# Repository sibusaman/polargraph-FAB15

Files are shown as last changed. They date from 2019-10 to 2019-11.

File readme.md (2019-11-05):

# Machines for Learning : The Wall Plotter
### **[Funded by The Hamdan Foundation, UAE](http://www.ha.ae/en/web/guest/home)**

During FAB15, 12 machines were built by the FabLab community and donated to 12 schools in Egypt. We made 
- 2 x mini CNC mill
- 5 x 3D printer
- 5 x Wall Plotter
  
The project was Funded by **[The Hamdan Foundation, UAE](http://www.ha.ae/en/web/guest/home)**.

The wall plotter design is mostly based on the [PolarGraph](http://www.polargraph.co.uk) machine. Here we document the slight differences in the design, the assembly instruction, software setup, calibration steps and other trouble shooting steps.

The machine was delivered in fully assembled and in fully working condition. Also the machine is very simple in terms of mechanical complexity. Which means detailed assembly instruction won't be necessary, as it is very trivial once the machine is in hand. The end users are supposed to hack these machines, modify, redesign..., so, we have provided some crucial information to help the end user do so. 

# Hardware

## BOM

The BOM is only for assembly, the end user do not need these as they already got the machine fully assembled.

- 2 x Nema 17 Bi-Stepper Motors 12v
- GT2 Timing belt, length depends on the machine dimension
- GT2 Pulley
- 1 x 9g 0-180 degree  Servo Motor, 
- 1 x Arduino Uno
- 1 x [CNC-Shield v3](https://blog.protoneer.co.nz/arduino-cnc-shield)
- 2 x Pololu, step-dir stepper driver or compatible
- A few jumpers (not wires), usually comes with stepper driver or CNC-shield
- 1 x 12v Power supply and 3-core power cable  
- Sufficient length of quality wire for 12v DC
- Wires for extending the stepper and servo motors.
- .
- m3,m4 and m6 nuts, washers and bolts of various lengths
- m15 washers or bolts or something similar to use as weights.
- zip-ties
- 3-5mm plywood sheet for laser cutting
- 12mm or more thick plywood/MDF sheet or similar. Dimension corresponds to the dimension of the final machine.
- Access to a 3D printer as there are a few 3D printed parts- 

## Mechanical Assembly 
- **Mounting the timing belt to the gondola :** The timing belt has to be attached with the Gondola by pinching the belt between the pen-holder (it has a small tooth corresponding to the timing belt tooth) and a small securing laser-cut retainer.
  - **The retainer** retainer
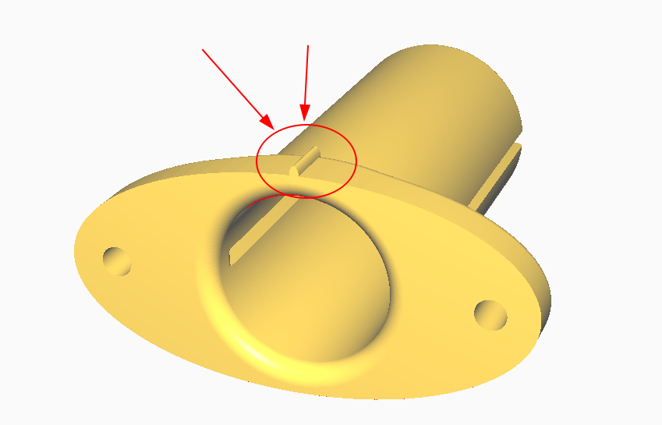
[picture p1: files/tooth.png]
tooth
  - **The tooth on the pen holder** 
  
- **Mounting the stepper motor :**  The stepper motor is mounted on a laser cut plywood. This assembly then goes onto the MDF/Plywood panel(used as the drawing board). 
  - If the laser cut plates are too flimsy, you may stack two of them.

  - The motor, in our case, is mounted to the plate using **m3** screws. It is recommended to use m3 washer, especially if you use soft plywood for the stepper mount plate.
  
  - The plate is then mounted to the big board using m5/m6 bolts, washers on both sided and nuts. 
  
  - There are alignment guides on the plates, there is a tiny hole to locate the corner of the board. Align this hole to the corner of the board. See the picture below.
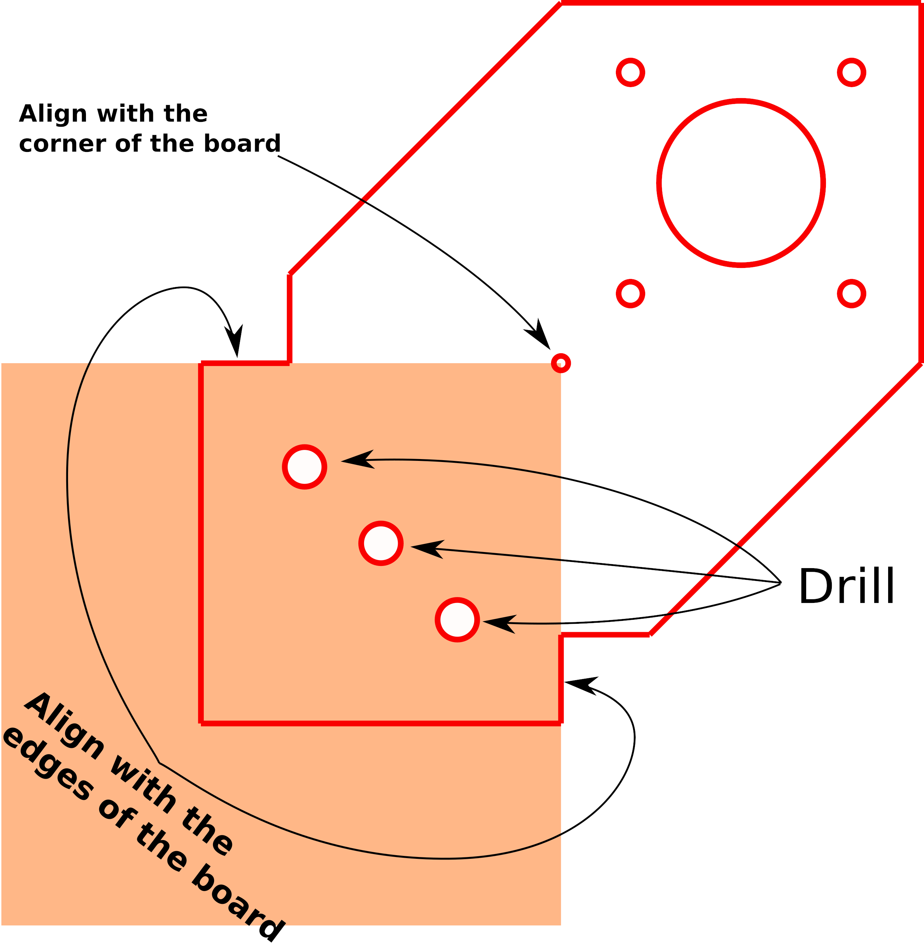
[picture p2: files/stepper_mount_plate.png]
stepper-plate
  - 
  
  - Then there are two right angle cuts, align these to the board edges. With these done, clamp the plate and drill the mounting holes on  the board. See the picture above.
  
- **Mounting the servo motor :**  The servo motor mount is designed to be used with small zip-ties. There are two sets of mounting holes. 
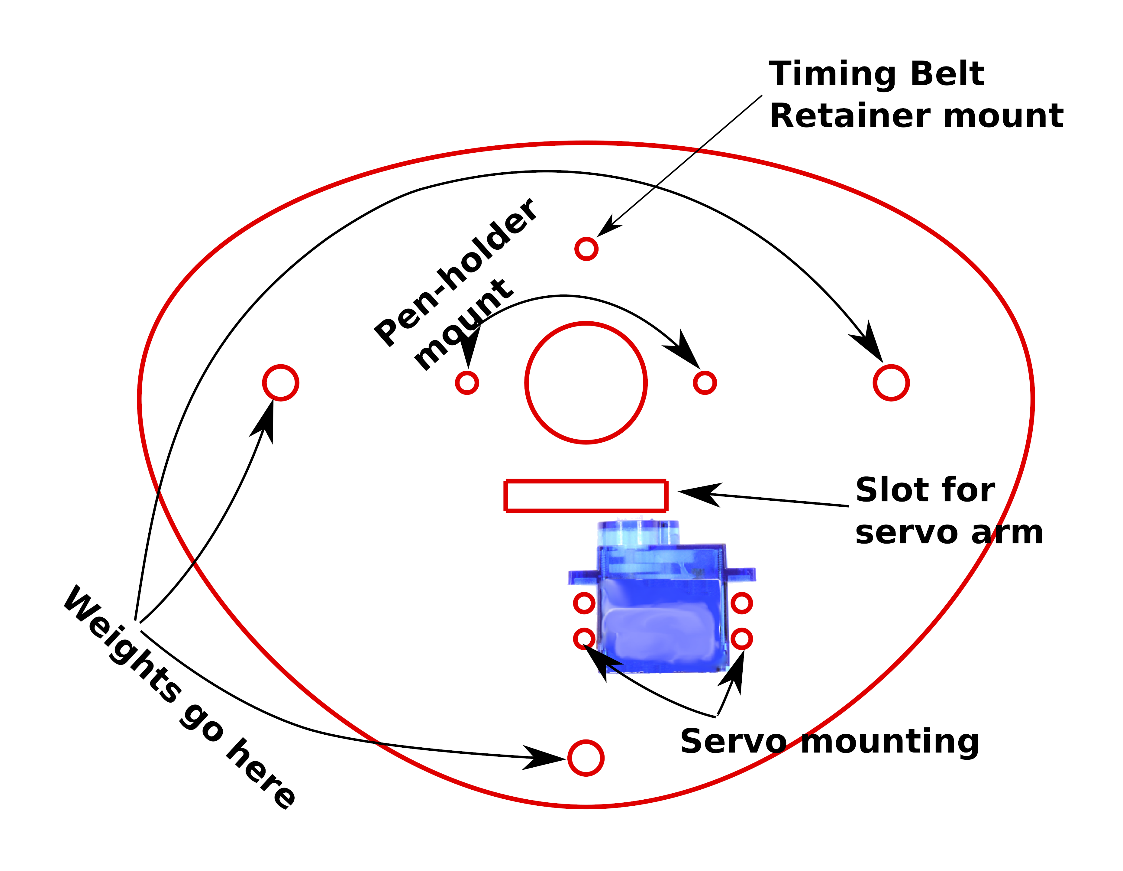
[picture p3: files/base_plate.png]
- 
  - The arm used is the single cam type.
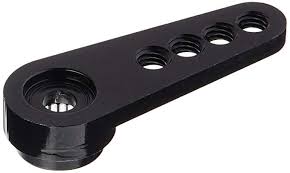
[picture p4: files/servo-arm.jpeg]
servo arm
  -  

  - **Mounting the servo arm** : Assuming that you have a 0-180 servo, not the continues rotation type. Connect the machine and do 'PEN-UP', at this position the arm should be mounted such that the arm touches the paper, raising the pen so that it doesn't touch the paper.  

  - If you have different types of servos you will have to play around and find the correct values for the PEN-UP and PEN-DOWN and edit the configuration file.

- **Attaching the counterweights :** There are three weights on the system. Two on either side. And one on the GOndola itself. 
  - The quick and dirty(and cheap) way I found to make a tunable counterweight is those 500ml water-bottles. The amount of the water tunes the weight. These are only for the ones on the side.

  - This can be done by making a small slit (with a sharp blade of course) on the cap, and inserting the timing belt through it. It will hold on it's on if you make the slit clean and just enough for the belt to enter through.

  - For the weight on the Gondola, it is recommended to use heavy steel nuts. This is clean and compact.

  - There are three place where you can mount these nuts on the gondola. One on the bottom and two on the sides. 
  **See the picture above**   

  - The long bolts used for mounting these nuts are actually thinner (**m5** or **m6**) than the nuts itself(often **m16** and higher, as  they are heavy). Because the bolt is mounted upside down and if we use **m16** bolt the head of this bolt will be too thick for the servo arm to be able to lift the pen. You can use m16 bolts, but then you will have to use longer servo arms and tune the servo parameters.

  - To secure the **m16** nuts on the thin bolts, you may cut washers from plywood.

- **Mounting the pen :** The pen holder will have to be modified for the pen you use, or  you will have to use some sort of grippy spacers, preferably rubber. You can also use rubber bands to increase the grip on the pen. The pen has to be mounted such that the tip just lifts up when the servo arm is engaged (pen-up position). [Here is the STL of the pen holder](./files/pen_holder.stl)
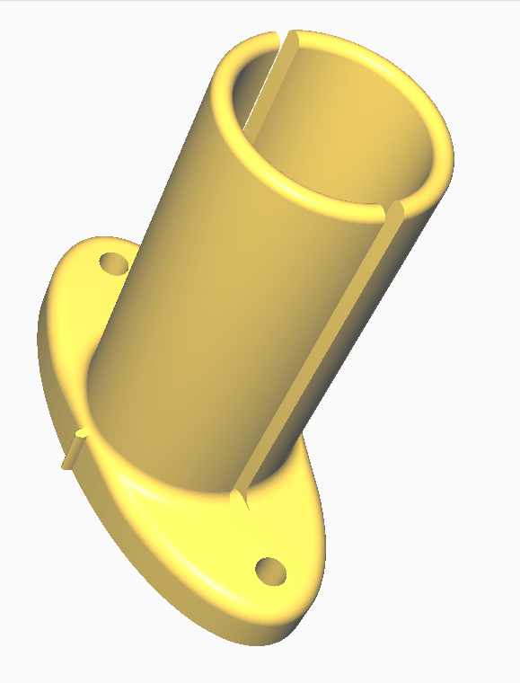
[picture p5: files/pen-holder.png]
pen-holder
- 

## Electronics 

### Connections
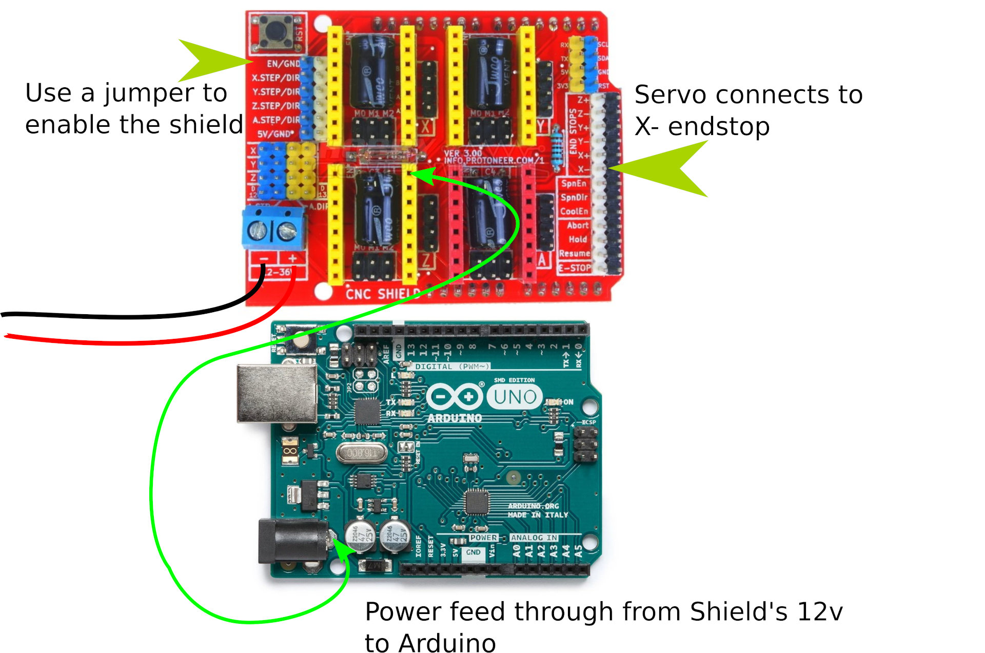
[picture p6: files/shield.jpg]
connections
- 
- **Servo connection :** The servo Wire need to be extended with Flat-Flexible-Cable FFC. The servo signal wire goes to the **PIN-9** of the arduino or **x- end-stop** in the shield. 

- **Micro-Stepping :** You can enable micro-stepping (I did, 1/16) for better resolution. 
- Stepper also need to be extended, but with wires that are rated for the maximum stepper current rating. Ethernet cables are cheap and readily available option. You get four pairs of wire from an ethernet cable, enough for both of the stepper motors. 

I used X and Y ports in the shield.

### Configuration
- **Enable jumper on CNC shield :** See the picture above. 

- **Power pass through from  CNC shield to Arduino :** See the picture above. This is required as the servo is powered by the 5v rail, which in turn comes from the Arduino board. The 500mA from the USB is insufficient to power the servo too.
 
  - This can be done with a wire with a male connector in one end, which connects to the **V_mot** pin of one of the unused stepper driver slots. The other end can be soldered to the positive out of the barrel connector, before the protection circuitry in Arduino.

  - Alternatively you can also split the 12v line, use a **5.5/2.1mm** barrel connector 

# Software

All the necessary files can be found in the repository. The Micro-controller firmware and Application can be found inside this [zip file](./files/Polargraph-2017-11-01.zip).

## Firmware and Tweaks

The folder, ```arduino-source``` have the firmware source.
Open it and copy the contents of the ```libraries```  into your arduino library folder (in linux, by default it is in ~/Arduino/libraries).

Also copy the ```polargraph_server_a1``` folder into the arduino project folder (````~/Arduino```` in linux).

There are few important edits to be made. 

- ```polargraph_server_a1.ino```
  - define the microcontroller (we have an UNO)
    - uncomment ```#define MICROCONTROLLER MC_UNO``` 
  - Choose the stepper driver type (we use pololu)
    - uncomment ```#define SERIAL_STEPPER_DRIVERS```
  - Disable unused features (optional)
  - define serial speed (57600 bps by default)
  - servo pin (we used default PIN9)
    - ```const byte PEN_HEIGHT_SERVO_PIN = 9;```
- ```configuration.ino```
  - step and direction pins for the controller
    ```bash
    #ifdef SERIAL_STEPPER_DRIVERS
   
    #define MOTOR_A_ENABLE_PIN 8
    #define MOTOR_A_STEP_PIN 2
    #define MOTOR_A_DIR_PIN 5
  
    #define MOTOR_B_ENABLE_PIN 8
    #define MOTOR_B_STEP_PIN 3
    #define MOTOR_B_DIR_PIN 6
    AccelStepper motorA(1,MOTOR_A_STEP_PIN, MOTOR_A_DIR_PIN); 
    AccelStepper motorB(1,MOTOR_B_STEP_PIN, MOTOR_B_DIR_PIN); 
    #endif
    ```

## Application and configuration
There is an UI for this machine and the application can be found inside the zip. The app is written an compiled using [processing 2.2.1](https://processing.org/download/). It does not work in version 3+.

The source code and pre-compiled binaries for Linux (and Windows, but I haven't tested this) are also provided in the zip.

The controller directory inside the zip have the compiled binary for the UI for the machine, for linux and windows. The default configuration file is named default.properties.txt, this can be replaced with custom config file. 

### Launching application
In linux, you need to make the ```polargraphcontroller``` file located in ```Polargraph-2017-11-01/controller/application.linux64/``` executable, by

```bash
chmod +x polargraphcontroller
```
Then launch the application by
```bash
./polargraphcontroller
```

### Loading custom config file 
The text file, [polar_custom.properties.txt](./files/polar_custom.properties.txt) is the configuration file for the UI and some aspects of the machine. There is a default config file, you can either replace it with the custom config file (and rename it) or load the custom file every-time you launch the application.
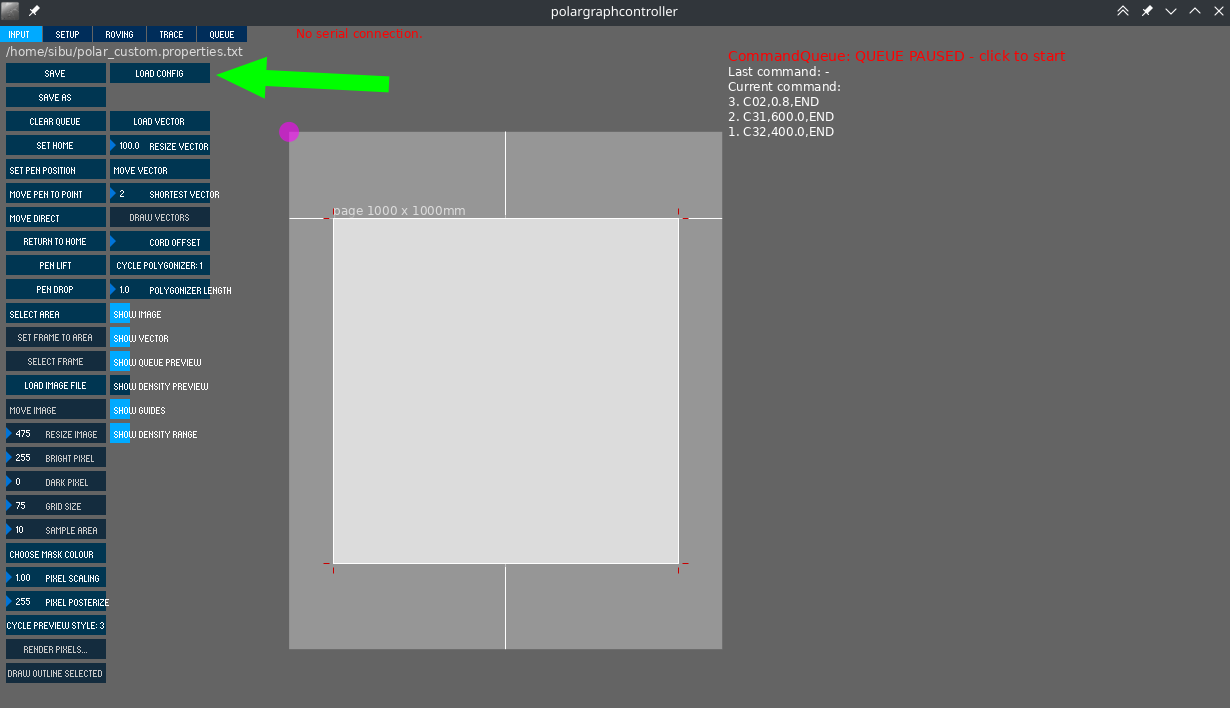
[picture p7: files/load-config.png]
config


        Note: Many of the machine configuration settings can be changed permanently by editing the polargraph_server_a1.ino , but still can be overridden by user configuration file. 

        Also the user configuration can be written to the micro-controller EEPROM from the application.

# Calibration and Tuning

## Calculating Steps/Rev
    Number of Steps to be sent to the step-direction based stepper controller for a full rotation of the shaft. 

This depends on the three parameters, 
- Micro-Stepping settings of the driver
- Number of full steps per rotation of the stepper motor, as specified in the motor specifications.
- Gear ratio if any

In our case we do not have any gear in the assembly, it's direct drive. So if the drivers are configured to be **1/N** Micro-Stepping, and the Motor is rated for **M** steps per rotation, 

**Steps/Rev = M x N**

    For our system this number is 200 x 16 = 3200 Steps/Rev

## Calculating mm/Rev
    This is the linear motion by the drive belt/string per rotation of the motor. In essence, it is the effective circumference of the final drive gear/pulley

For a system with timing belt,
This number depends on the number of gear pitch and number of gears on the drive pulley. 

**(Pitch) x (Number of gear on the drive gear)**

    For our system, we are using a 20 tooth GT2 pulley to drive the GT2 belt, so, this number is 20 x 2 = 40mm/Rev

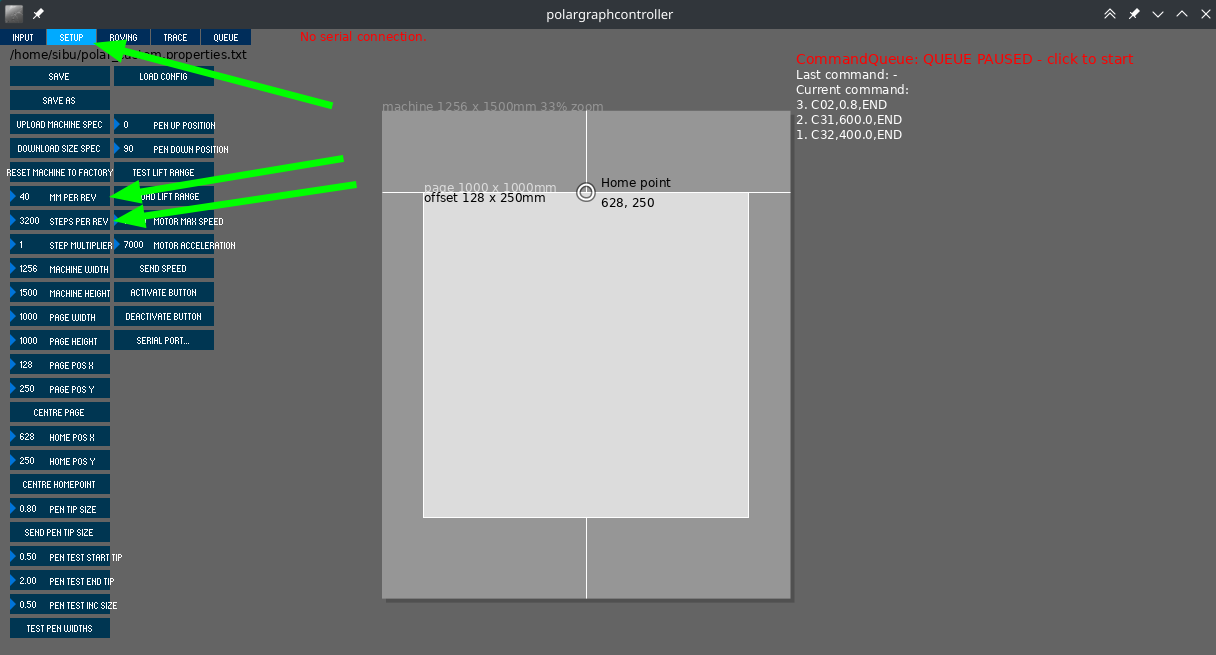
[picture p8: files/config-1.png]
config-1
 
 You can change the defaults in the configuration file.

## Max speed and acceleration 
The max speed and acceleration is to be found out by the user and it varies from machine to machine. It depends on several factors like, 

- The Torque rating of the motor

- Power-supply 

  - supplying 12v to to a 24v rated motor won't give you the ideal performance

- Stepper motor controller

- Micro-stepping configuration

- The tensioning weights used 

  - more weight means less acceleration for a given torque
  
  - but, less weight will make the belt slip from the gear
  
  - less weight also means less pen force.

These parameters can be found by trial and error. The crude way os to find the settings at which it fails and turn it down a bit.

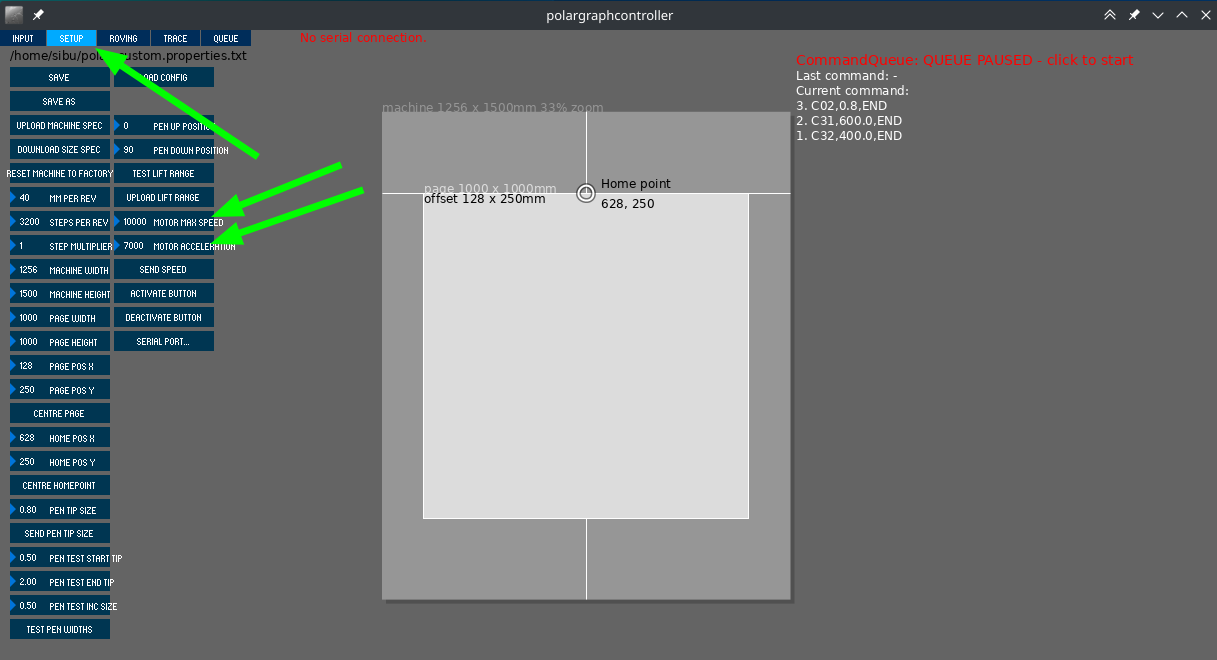
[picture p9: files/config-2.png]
config-2
 

## Setting zero

**This could be the most crucial step of the entire assembly.** Where you set the origin in the machine is super important in polar machines to make the machine where move the way you want. Read the note below to understand why.

    Note: The important thing to understand is that the machine is working in polar coordinates. 
    
    Let's call 
    - X and Y as the machine head position.
    - dx and dy as the change in X and Y we need
    - m1 and m2 as the rotation in motor 1 and 2 to make the change dx and dy.
    
    In traditional cartesian coordinates, no matter where your head is at you can ask the machine to move dx and dy and it will move exactly dx and dy. In a way in cartesian machines the motion of the head is only a function of the motion of the motor shafts, m1 and m2 and not the current positions itself.

    Even in unconventional cartesian machines like H-bot or CORE-XY, the dx and dy is only a function of m1 and m2.

    dx,dy = f(m1,m2)

    But for polar machines like this. dx and dy is a function of m1,m2,X and Y

    dx,dy = f(m1,m2,X,Y)

As you see in the note above, in this machine calibration is extremely important, else you will get a distorted drawing. For example, you may want to draw a square and if your calibration is wrong, you may end up with some wired shape with curved edges.

There are few measurements and configuration settings you have to do before setting zero.

We need to measure the 
- **Machine dimension (Width and Height) :**  
  - **The width** of the machine is measured from the left anchor point of the belt to the right anchor point of the belt. we can approximate this by **shaft to shaft** length. 
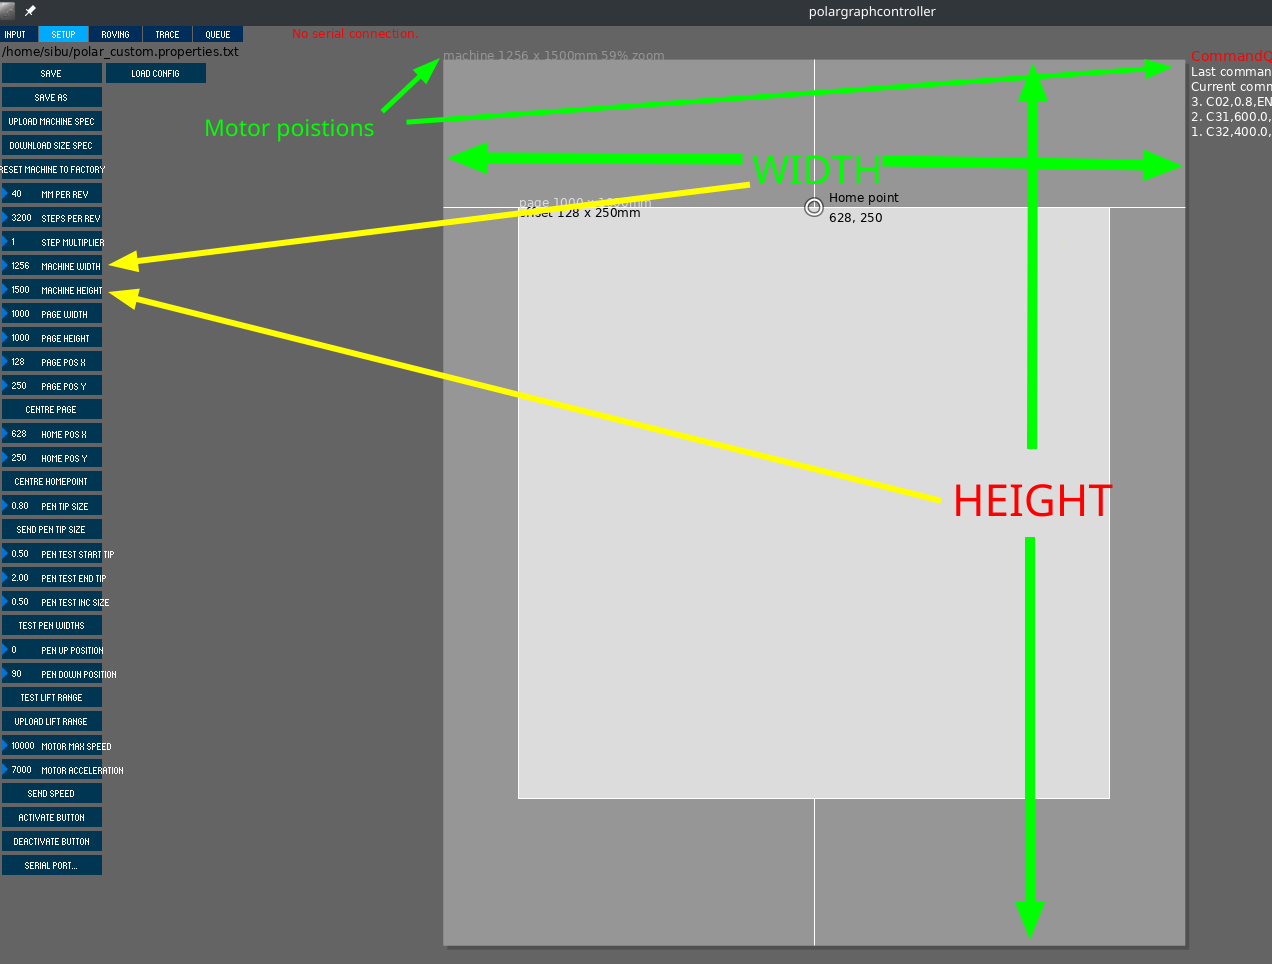
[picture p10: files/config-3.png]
config-3
    - 

  - The height of the machine is not that critical, means it doesn't affect the performance of the machine. But set it as the height of the MDF/Plywood drawing platform.

- **Page Dimensions :** This is the WIdth and Height of the page/paper in which we are drawing. 
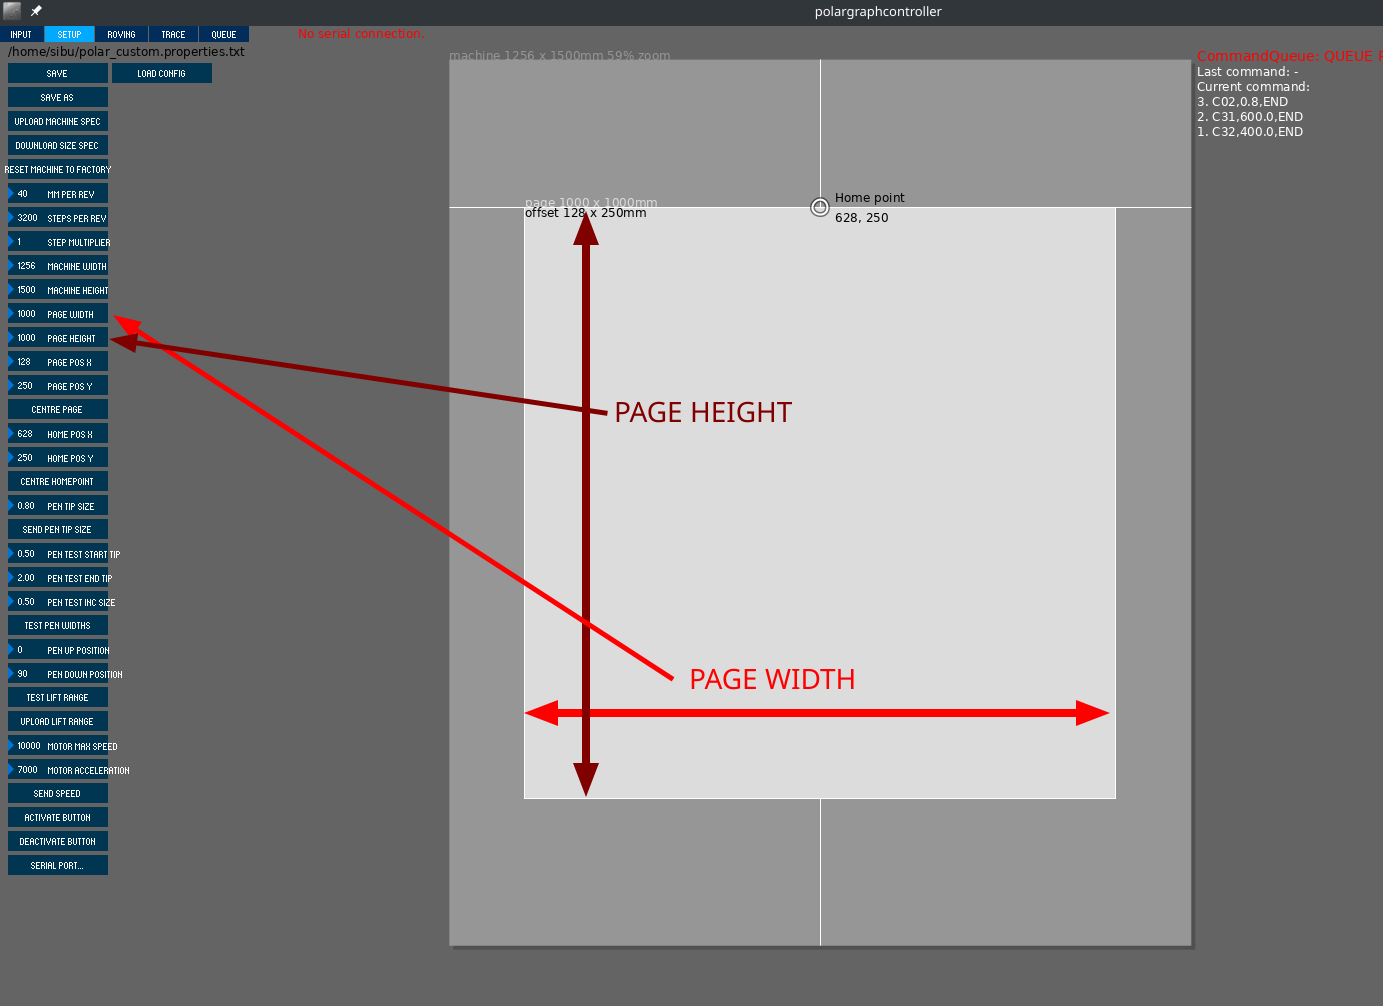
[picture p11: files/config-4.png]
config-4
  - 

- **Page position :** This is the XY offset of the page with respect to the top left motor shaft. Try to keep the page centered in X. For Y, keep it slightly below the Y=0 line (line connecting shaft to shaft), otherwise the machine will have to generate very high tension to raise the pen to the top of the page and  this will most likely result in slippage of the belt from pulley and loose calibration.
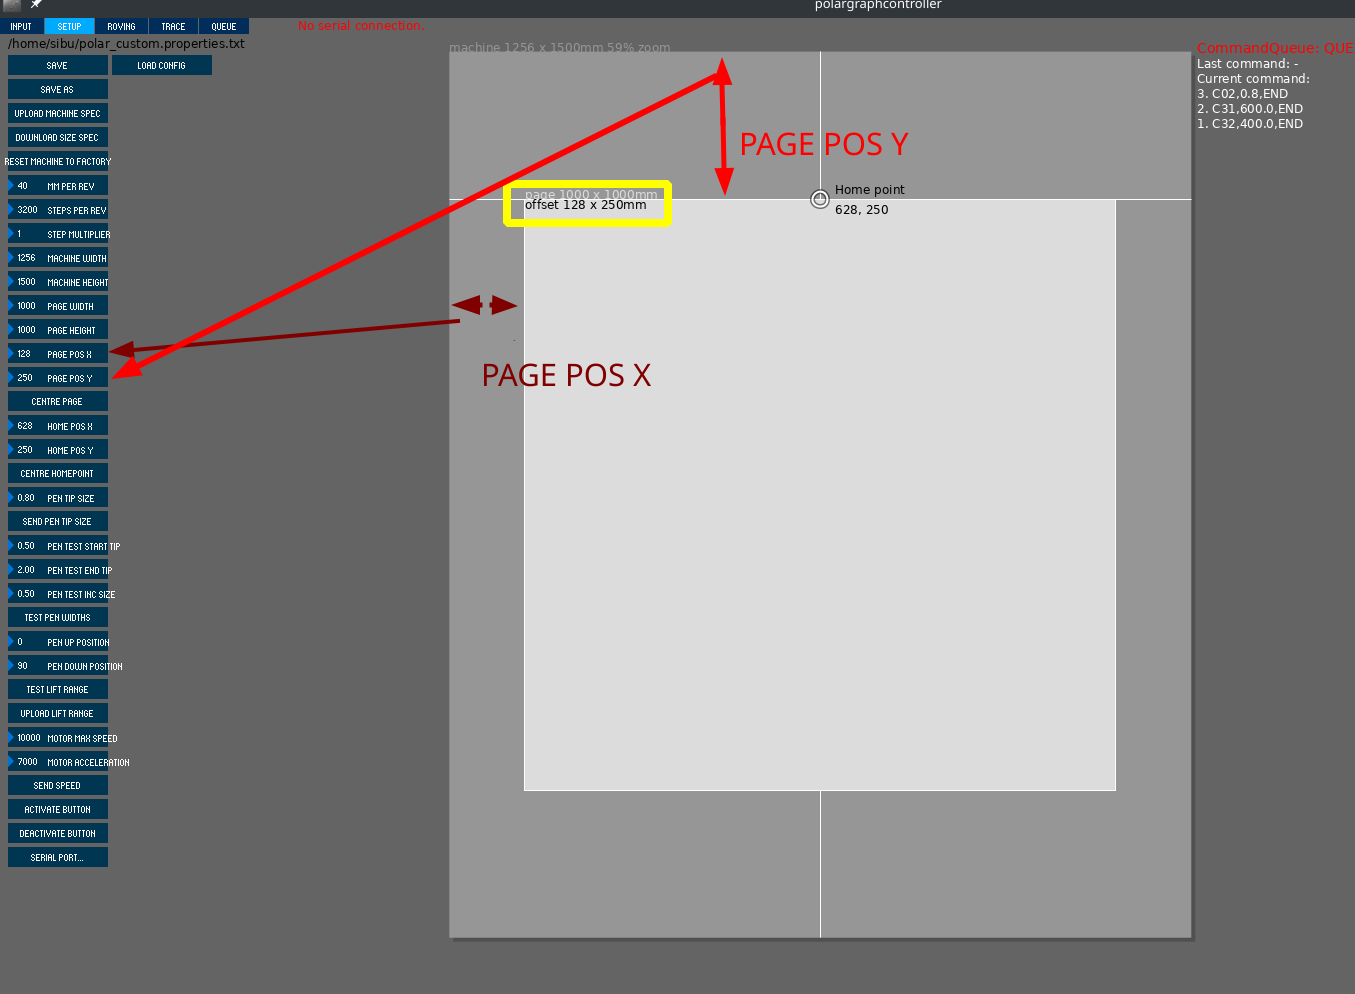
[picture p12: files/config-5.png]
config-5
  - 

The way I do the calibration is to choose a point, half of the width of the machine/board and at the top of the drawing area. Permanently mark this spot on the board with a tiny hole or a screw or something. Measure this point with the top left motor shaft as the origin. 
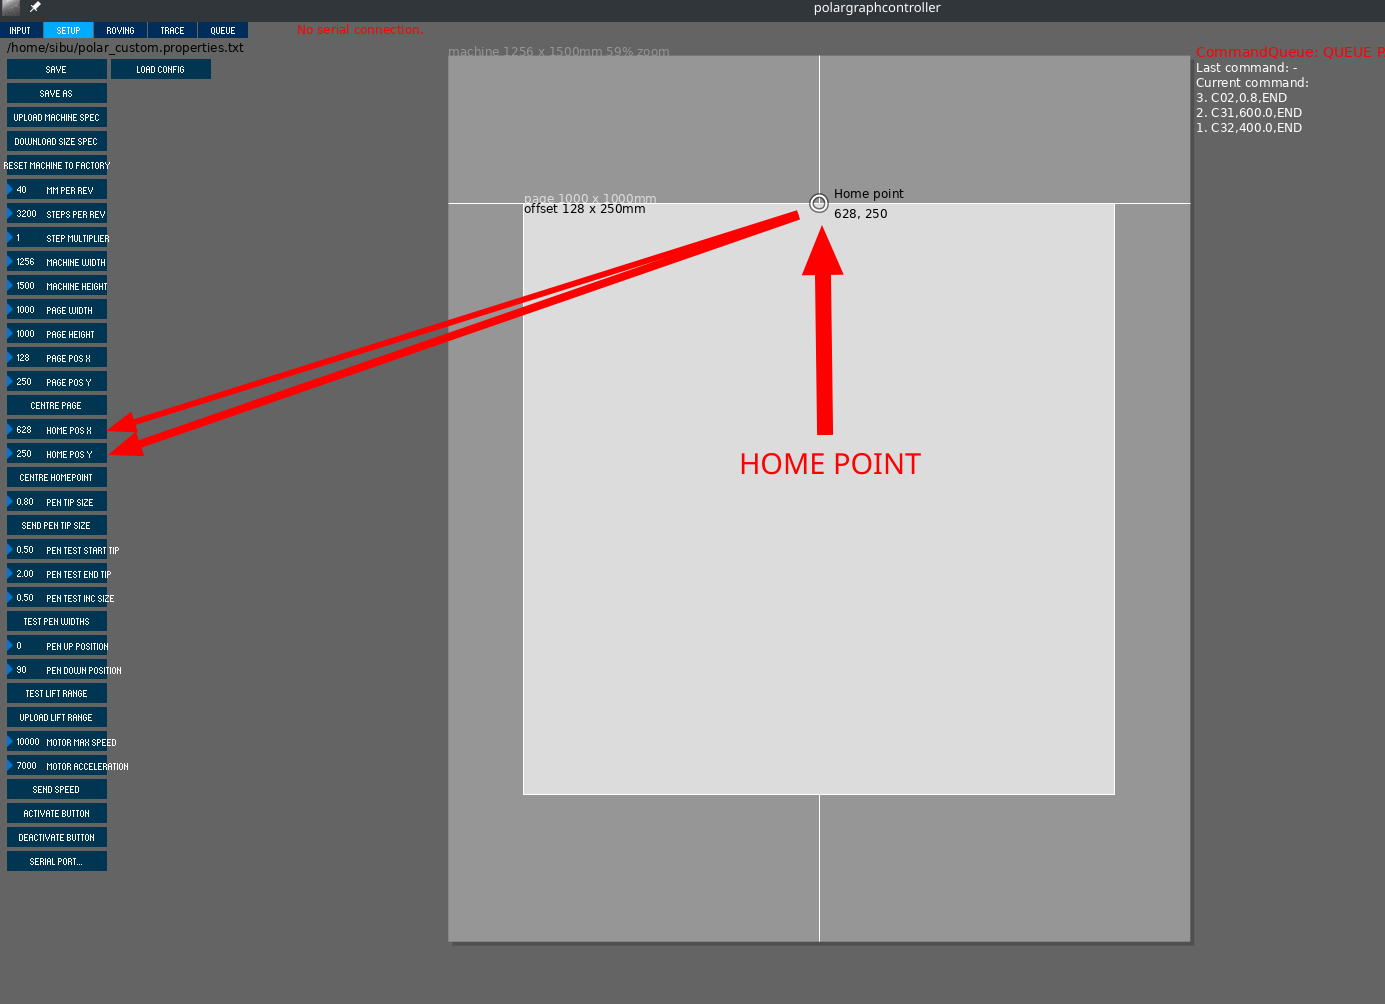
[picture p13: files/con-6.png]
con-6
 

- The HOME_POINT Y is same as the PAGE_OFFSET is you do it right. 
- The HOME_POINT X is Machine_Width / 2 
  
- Now, to actually set the Home, 
    - disable the power to the stepper, 
    - click set home, the motors will not move, but the machine will assume that it moved to HOME_POINT.
    - bring the machine manually to the HOME_POINT and engage the power to the stepper.
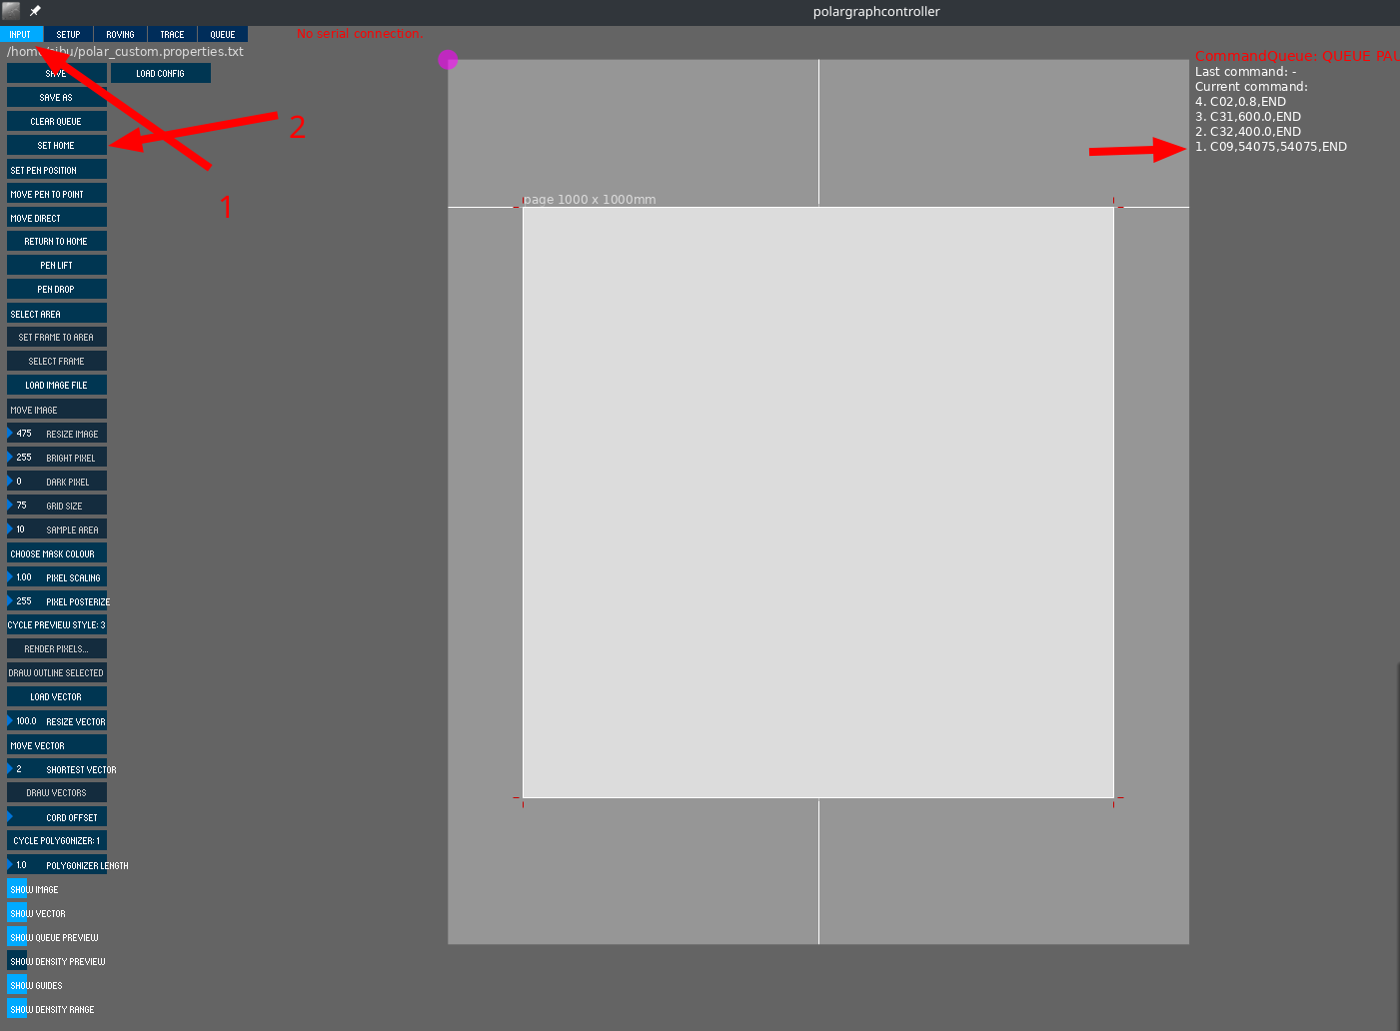
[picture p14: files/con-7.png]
con-7
    - 

# Draw
Now we are done with the hard part. Load a vector and draw. 

- Load vector with the LOAD_VECTOR button
- Move vector by clicking MOVE_VECTOR button and then dragging the center of the vector where you want it.
- Scale the vector by **moving the mouse up or down while clicking and holding the SCALE_VECTOR button**.

# References 

## All mechanical CAD was made by OnShape and the are [available HERE](https://cad.onshape.com/documents/d169351ce7a3db9697c065e0/w/642eb27db53fa1065eb8dde2/e/45781a3c8a8712fb6f7df40b)

- [PolarGraph](http://www.polargraph.co.uk) website
- [Polargraph Wiki](https://github.com/euphy/polargraph/wiki)
- [CNC-shield](https://blog.protoneer.co.nz/arduino-cnc-shield/)
- [Inscrutable article](https://www.instructables.com/id/Polargraph-Drawing-Machine/)
- [Latest Controller Software](https://github.com/euphy/polargraphcontroller/releases/tag/2017-11-01-20-30)

#
#
#

# Limitations and improvements to be made

- Gondola and pen holder
  - The current design is only compatible with one type of pen. There are better designs using more expensive or difficult or get parts. But they may perform better.
- End-stops (Most plotters like this does not have end stops and homing, but it should be doable with a little modification to the firmware)
- Power supply upgrade or Stepper motor upgrade: 
  - The power supply was 12v, but the available stepper motors are rated for 24v. Which means we are not getting the rated torque. We should wither use 24v supply, or 12v rated motor. I recommend the later, as we are using a builtin 5v linear regulator in Arduino to generate the 5v, doing this with 24v is not efficient and safe.

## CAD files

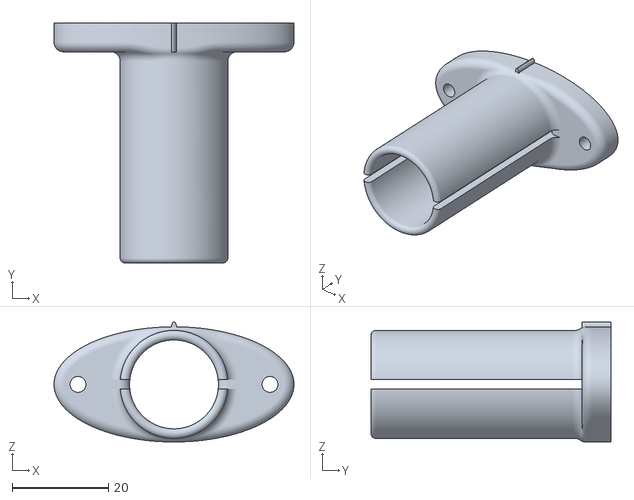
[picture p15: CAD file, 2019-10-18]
files/pen_holder.stl
50.0 x 50.0 x 25.0
